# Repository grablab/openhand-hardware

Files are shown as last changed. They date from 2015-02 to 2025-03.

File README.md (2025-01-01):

Yale OpenHand Project - Hardware
=======

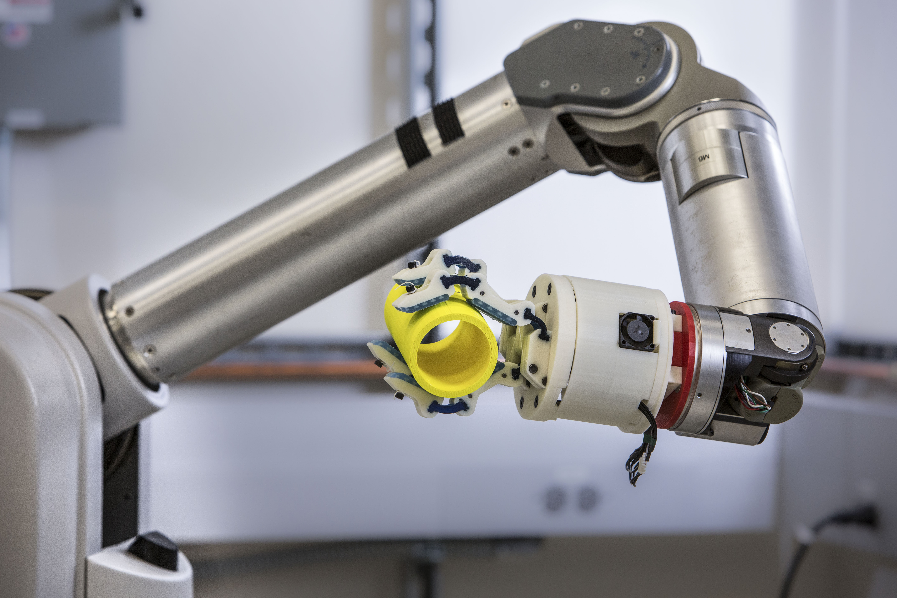
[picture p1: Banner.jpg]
Yale Openhand


CAD files for the various OpenHand hardware designs. Complete documentation, including assembly directions, can be found on the [OpenHand website](http://www.eng.yale.edu/grablab/openhand/). Control code for the most widely used hands (Model T, Model T42, Model O), with addition to a ROS node, can be found on our [openhand_node](https://github.com/grablab/openhand_node) page. For simply printing a certain hand model, navigate to the folder of the same name, and all the parts can be found in the .stl folder. For modifying the SolidWorks files, all hand-specific parts and assemblies are located inside of the hand’s folder (with exception of the M2 and VF, which share the same base as the T42). Additional parts can be found within /fingers, /couplings, or /common parts. 

All hands follow the same naming conventions with exception of Model Q. A basic dictionary of part names follows: 
a*_handName: Larger pieces used for structure. Ordered from top of the hand to the bottom. 
b*_handName: Smaller gear or servo attachment pieces. 
c*_handName: Finger mounts.
d*_handName: Optional pieces.

Most of the hand designs come with multiple finger options, each using a combination of flexure and pivot joints. Flexure joints are created with Smooth-On urethane rubber either using cut-away thin wall molds or multi-part, reusable molds. Details on Hybrid Deposition Manufacturing to create flexure joints and finger pads can be found [here](https://www.eng.yale.edu/grablab/openhand/hdm.html). 

Things to note:
- Most Solidworks parts have dependencies on other parts. To avoid warnings/errors when opening assemblies, be sure to have "Load referenced documents" set to "All" in Options>>External References
- Many of the assemblies use Configurations extensively to cut down on the number of CAD source files I have to maintain. Be sure to check them out!
- More details about our approach to CAD for this project can be found in our [CAD Guide](http://www.eng.yale.edu/grablab/openhand/OpenHand%20CAD%20Guide.pdf)

### Model T
Based on the original SDM Hand [[1]](https://www.eng.yale.edu/grablab/pubs/Dollar_IJRR2010.pdf), the Model T is the OpenHand Project's first released hand design. The four underactuated fingers are differentially coupled through a floating pulley tree, allowing for equal force output on all finger contacts. Due to the limitation of having only one actuator, this hand lacks in-hand manipulation capabilities, but excels in tasks requiring adaptable gripping with limited actuation [[2]](https://www.eng.yale.edu/grablab/pubs/Ma_RAM2017.pdf), [[3]](https://www.eng.yale.edu/grablab/pubs/Ma_ICRA2013.pdf)

### Model T42
The Model T42 is a two-finger, two-actuator hand designed for more dexterous planar tasks. It is still capable of underactuated, adaptive grasping, but the additional actuator makes it capable of some in-hand manipulation primitives as well as precision grasping, e.g. [[4]](https://www.eng.yale.edu/grablab/pubs/Calli_TASE2018.pdf), [[5]](https://www.eng.yale.edu/grablab/pubs/Sintov_RAL2019.pdf). 

### Model M2
The Model M2, short for Multi-Modality Gripper, is a minimalist gripper with a single underactuated finger and a library of modular thumb designs. Each thumb design can enable a different grasping behavior and allows for faster, more versatile design iterations. The distinct agonist and antagonist tendons allow for both underactuated and fully-actuated grasps of objects. By sacrificing the full-actuation capabilities of the M2, the Model M functions otherwise identically with only one actuator [[6]](https://www.eng.yale.edu/grablab/pubs/Ma_REMAR2015_1.pdf).

### Model VF
The Model VF, short for Variable Friction Gripper, is similar to the T42 with the addition of changing finger pad surfaces. The additional actuator within each finger allows the hand to change surface friction during manipulation. By swapping the Constant and Variable Friction fingers, the hand can translate and rotate objects in a controlled manner [[7]](http://berkcalli.com/publications/2018-SpiersCalliDollar.pdf).

### Model O
The Model O is a three-finger, four-actuator hand designed to replicate the capabilities of commercial hands such as [BarrettHand](http://www.barrett.com/robot/products-hand.htm), RightHand Robotics' [Reflex Hand](http://www.righthandrobotics.com/main:reflex), and Robotiq's 3-Finger Adaptive Gripper. Each underactuated finger is independently controlled, while a fourth actuator controls the adduction/abduction angle between two of the fingers. This allows the hand to transition between spherical-grasping and power-grasping configurations [[8]](https://www.eng.yale.edu/grablab/pubs/Odhner_IJRR2014.pdf).

### Stewart Hand
The Stewart hand is a dexterous hand designed for 6-DOF within-hand manipulation. Its non-anthropomorphic design draws inspiration from the Stewart-Gough platform parallel mechanism. This simple kinematic structure allows for straightforward, accurate control with minimal sensing [[9]](https://www.eng.yale.edu/grablab/pubs/McCann_RAM2021.pdf).

### Model Q
The Model Q is a four-finger, four-actuator hand similar in actuation elements to the Model O, but vastly different in capabilities. The two independently-actuated precision-grasp fingers allow for pinching similar to the Model T42’s capabilities. A pair of power-grasping fingers are controlled by a single actuator, while also being rotated with respect to the precision-grasping fingers by a fourth actuator. This setup enables in-hand finger-gaiting by trading control of the manipulated object between the two pairs of fingers while rotating the power-grasping set. Using its two independent sets of fingers, the hand can also manipulate an in-hand object closer to its palm for a tighter power grasp [[9]](https://www.eng.yale.edu/grablab/pubs/Ma_ROBIO2014.pdf).

### Model F3
The Model F3 is an adaptation of the flexure-flexure version of Model T42. This hand is designed to enable contact force estimation based on gripper deformation using a wrist-mounted camera. Length and angle of the finger links have been changed to avoid singularities upon contact at the fingertip. Tendon routing and motor positions are optimized to significantly reduce tendon friction which allows for more accurate force predictions. (publication under review)

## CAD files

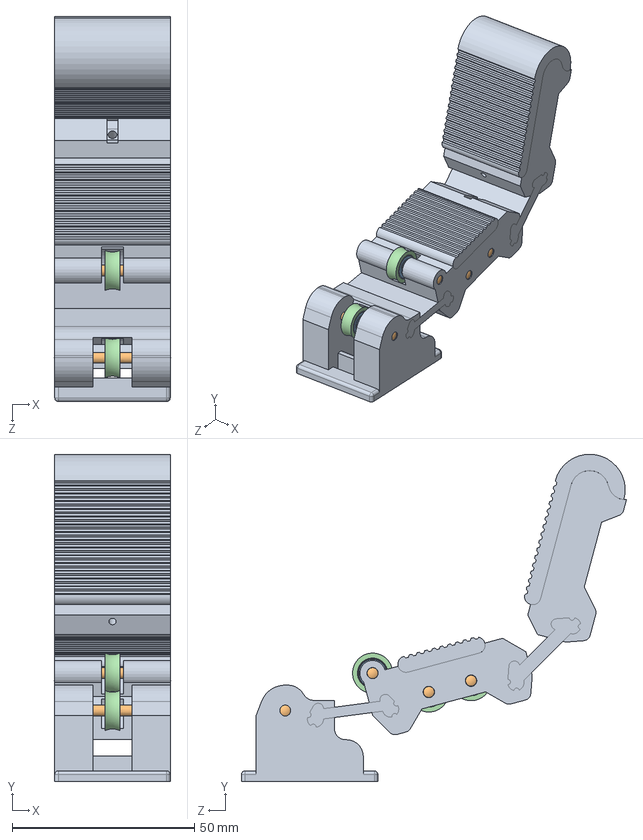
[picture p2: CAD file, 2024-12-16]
model f3 (forces-for-free hand)/F3_finger_assembly.SLDASM
32.0 x 89.9 x 105.7 mm
F3_finger
91595A138_Dowel Pin x 4
7804K126_Stainless Steel Ball Bearing x 4
bearing_sleeve x 4

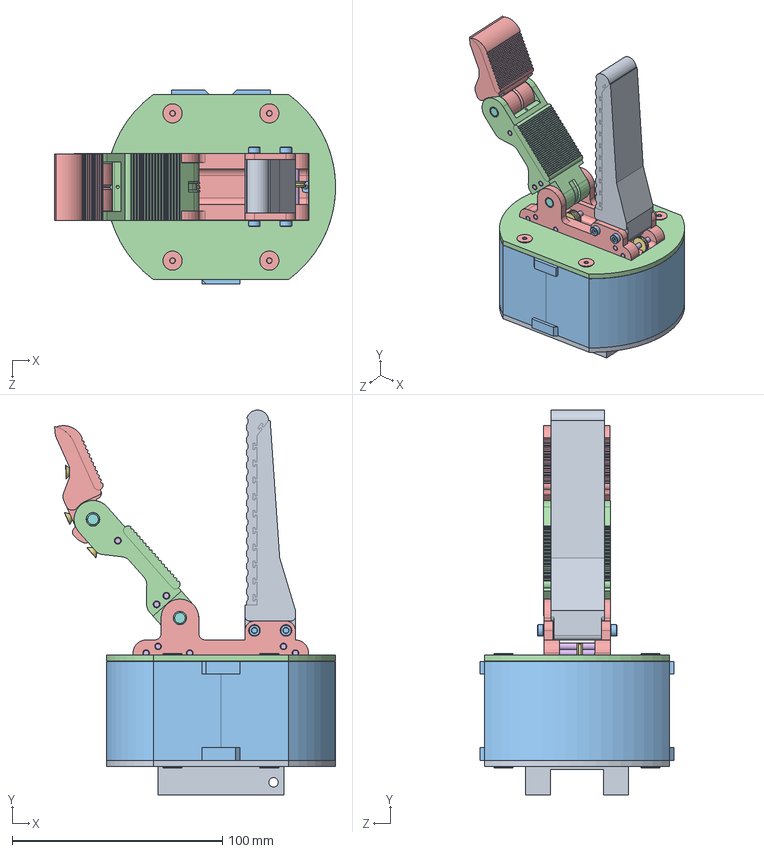
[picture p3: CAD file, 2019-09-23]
model m2/hand_m2.SLDASM
133.7 x 183.0 x 92.0 mm
a4_t42
a3_t42
a2_t42
93330A440 8-32 L3-2 standoff x 4
92210A197 8-32 L3-4 countersunk x 8
fan - 25x25x7
dynamixel XM-430 x 2
91290A012 M2 L5 socket x 4
b1_t42 x 2
d2 x 2
d1_t42_fan x 2
a1_t42
c1_m2
98381A477 D1-8 L5-4 x 8
3434T31 - nylon pulley x 4
98381A544 D1-4 L5-4 x 2
thumb1
94180A333 M3 insert x 4
91292A112 M3 L8 socket x 4
m2_pp_A
t42_pp_B
93365A120 4-40 insert x 3
91253A106 4-40 L1-4 countersunk x 3

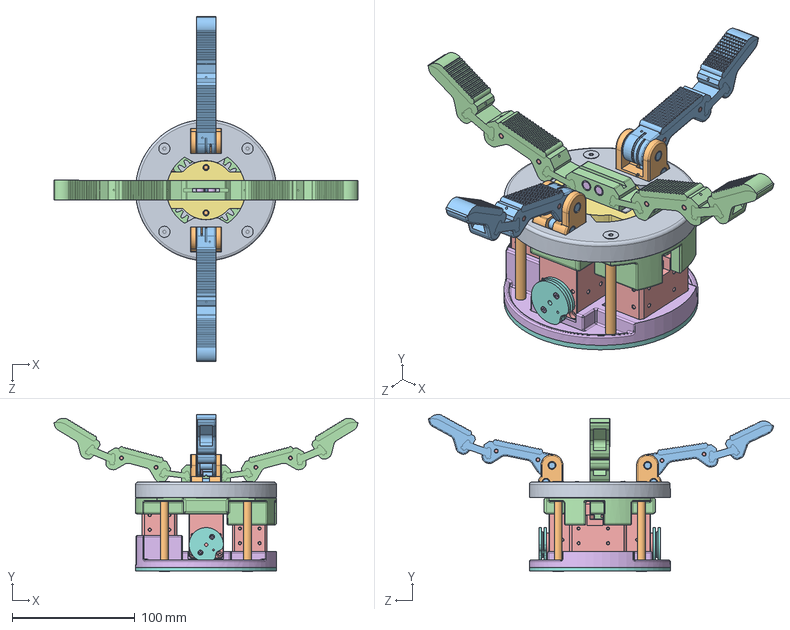
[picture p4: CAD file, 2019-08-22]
model q/hand_q.SLDASM
248.0 x 128.1 x 281.6 mm
top_outer
pivot_base x 2
98381A542 D1-4 L1 x 4
q_ffff
98381A472 D1-8 L5-8 x 8
98381A539 D1-4 L5-8 x 2
top_inner
93365A130 6-32 insert x 2
gear_main
92196A146 6-32 L3-8 socket x 2
q_pf x 2
mid_clamp
dynamixel XM-430 x 4
91290A012 M2 L5 socket x 5
gear_motor
horn2 x 2
92210A197 8-32 L3-4 countersunk x 8
93330A483 8-32 L2 standoff x 4
3434T31 - nylon pulley
pulley_block_half x 2
97395A435 D1-8 L3-8 x 3
bottom_no_bridge
bottom_reroute
bottom_brace_insertv2

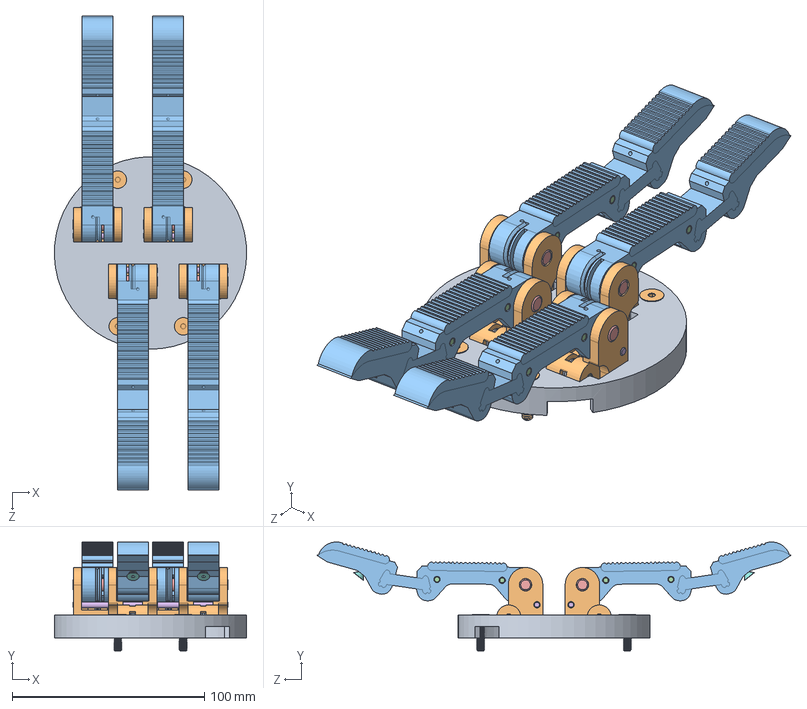
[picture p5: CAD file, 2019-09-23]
model t/MX64/block_top_pf_t.SLDASM
100.0 x 56.7 x 246.5 mm
a1_p_t
c1_t x 4
t_pf x 4
98381A472 D1-8 L5-8 x 12
98381A542 D1-4 L1 x 4
98381A475 D1-8 L1 x 4
93365A120 4-40 insert x 4
91253A106 4-40 L1-4 countersunk x 4
3434T31 - nylon pulley x 4
92210A197 8-32 L3-4 countersunk x 4

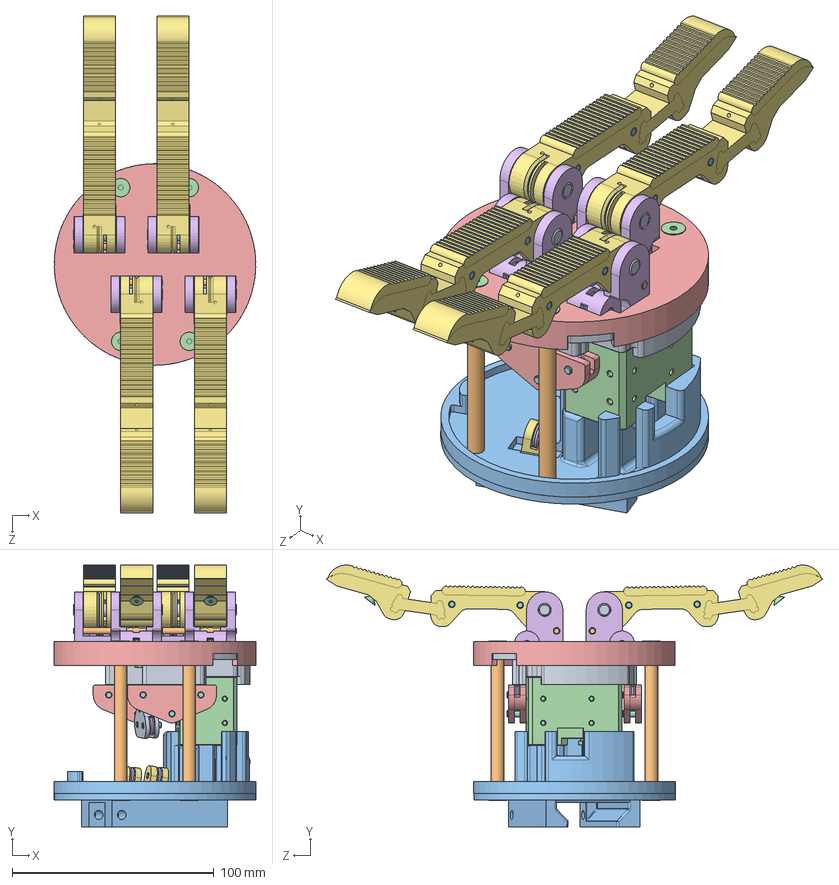
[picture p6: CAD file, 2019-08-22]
model t/XM430/hand_t_pf.SLDASM
100.0 x 129.9 x 246.5 mm
a2_t
b6_t
a3_t
dynamixel XM-430
b1_t
3434T31 - nylon pulley x 13
b2_t x 2
97395A435 D1-8 L3-8 x 11
b5_t x 2
92474A029 8-32 L5-2 standoff x 4
a4_t
92210A197 8-32 L3-4 countersunk x 8
b3_t x 4
c1_t x 4
t_pf x 4
98381A472 D1-8 L5-8 x 12
98381A542 D1-4 L1 x 4
98381A475 D1-8 L1 x 4
93365A120 4-40 insert x 4
91253A106 4-40 L1-4 countersunk x 4
a1_p_t
91290A012 M2 L5 socket x 2

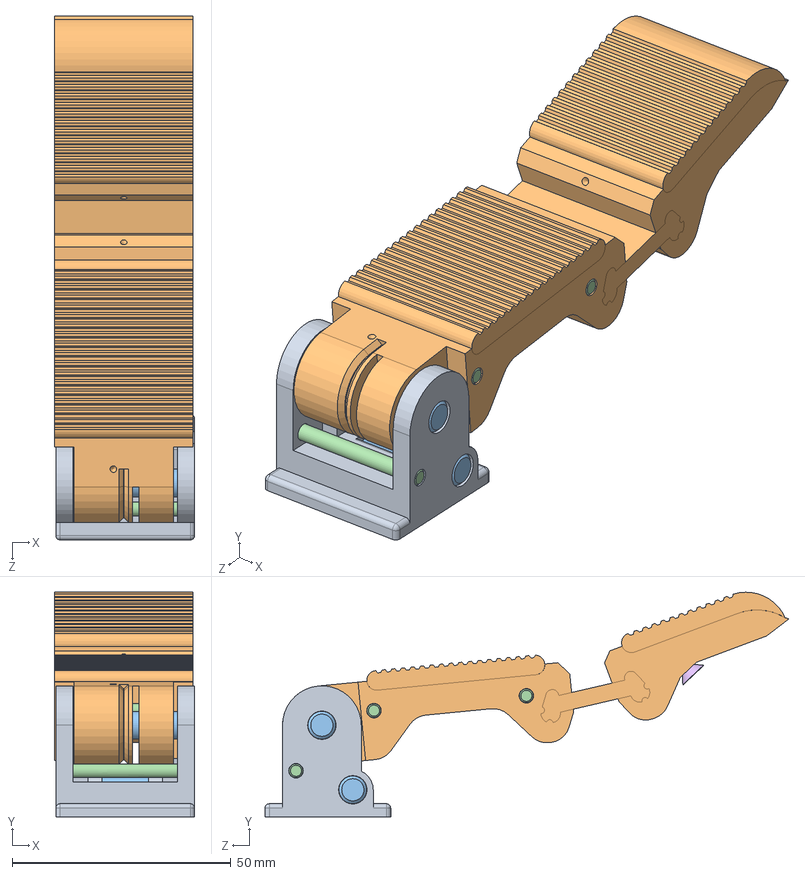
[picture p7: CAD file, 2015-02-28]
model t42/edrawings/block_finger_pf_t42.SLDASM
32.1 x 51.3 x 119.8 mm
c1_t42
finger_pf_t42
98381A544 D1-4 L5-4 x 2
98381A477 D1-8 L5-4 x 3
93365A120 4-40 insert
91253A106 4-40 L1-4 countersunk

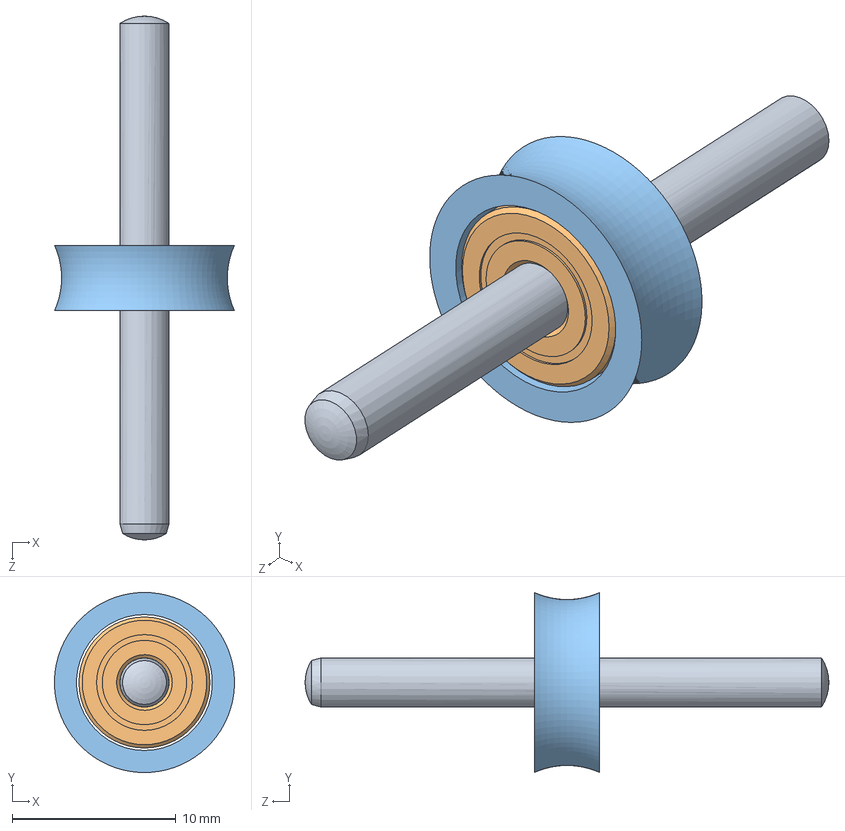
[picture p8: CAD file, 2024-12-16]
model f3 (forces-for-free hand)/sldprt/pin_bearing_assembly.SLDASM
11.0 x 11.0 x 32.0 mm
91595A138_Dowel Pin
7804K126_Stainless Steel Ball Bearing
bearing_sleeve

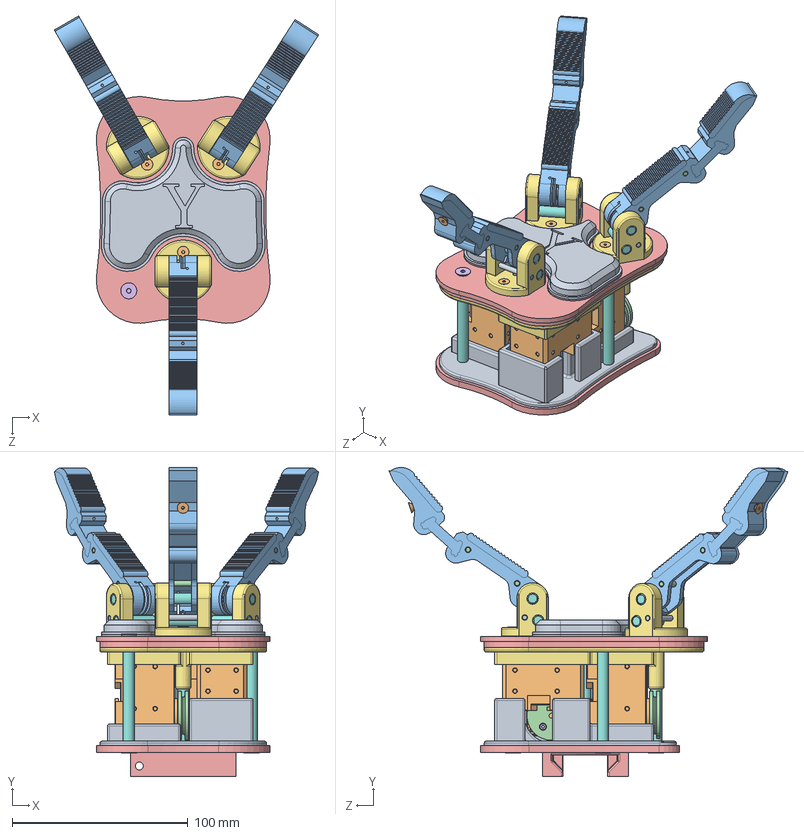
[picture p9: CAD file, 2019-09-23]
model o/XM430/hand_o_pf.SLDASM
150.6 x 176.0 x 227.2 mm
d3_o_minimal
93365A120 4-40 insert x 11
91253A110 4-40 L1-2 countersunk x 2
c2_left_o
c2_right_o
b3_o x 2
c1_o x 3
98381A544 D1-4 L5-4 x 6
98381A477 D1-8 L5-4 x 3
91253A106 4-40 L1-4 countersunk x 9
finger_pf_t x 3
98381A472 D1-8 L5-8 x 6
a1_o
92210A197 8-32 L3-4 countersunk x 8
a2_o
93330A483 8-32 L2 standoff x 4
a3_o
dynamixel XM-430 x 4
b2_o
b1_o x 3
a4_o
91290A012 M2 L5 socket x 6

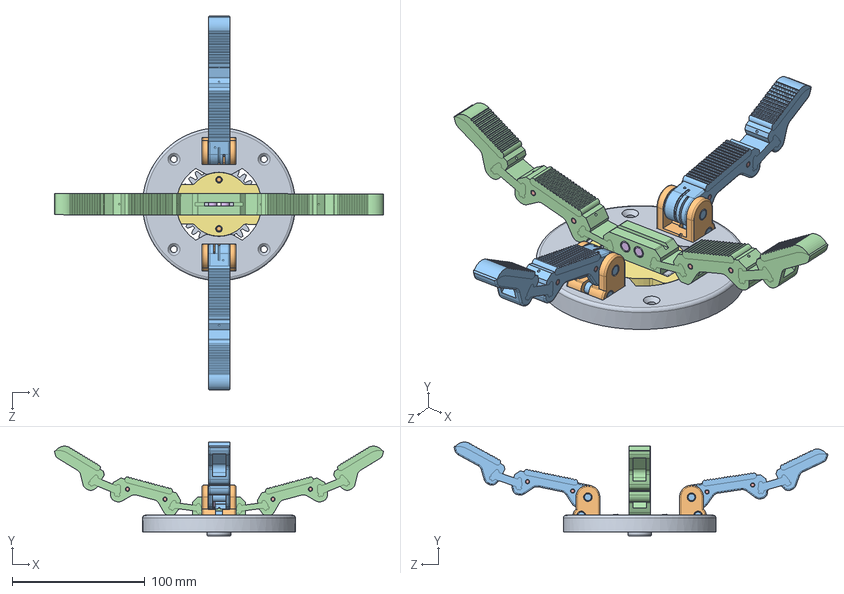
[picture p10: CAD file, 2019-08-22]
model q/asm_upper_hand.SLDASM
248.0 x 70.8 x 281.6 mm
top_outer
pivot_base x 2
98381A542 D1-4 L1 x 4
q_ffff
98381A472 D1-8 L5-8 x 8
98381A539 D1-4 L5-8 x 2
top_inner
93365A130 6-32 insert x 2
gear_main
92196A146 6-32 L3-8 socket x 2
q_pf x 2

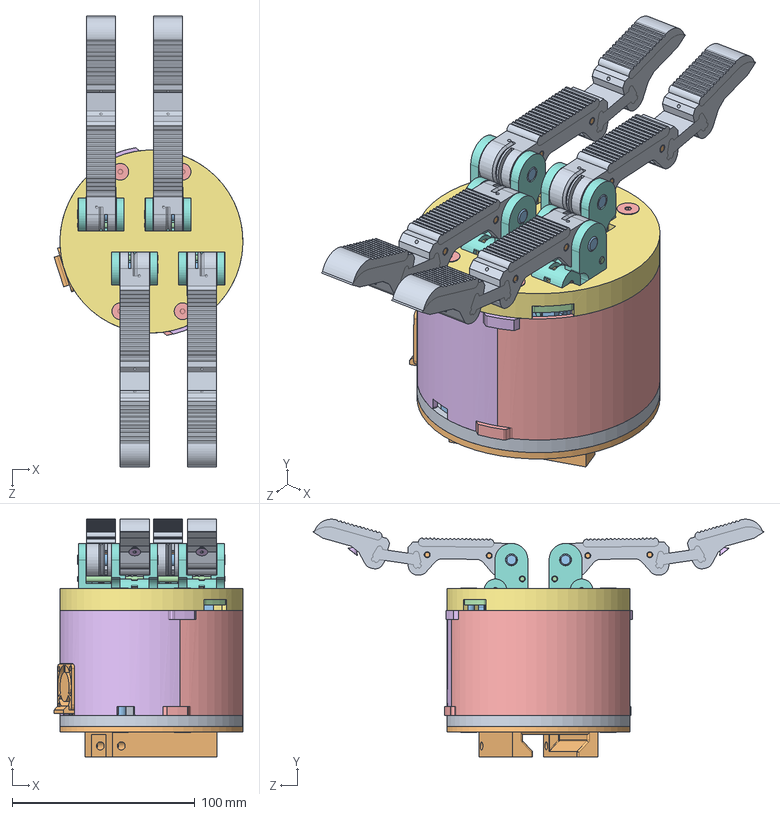
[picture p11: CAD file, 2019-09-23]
model t/MX64/hand_t.SLDASM
103.2 x 129.9 x 246.5 mm
a3_t
a4_t
92474A029 8-32 L5-2 standoff x 4
a2_t
92210A197 8-32 L3-4 countersunk x 8
b2_t x 2
3434T31 - nylon pulley x 14
97395A435 D1-8 L3-8 x 13
dynamixel-MX-64-exposed
d2_t
91772A266 2-56 L5-4 pan x 4
b1_t
91292A112 M3 L8 socket
b4_a_t
b4_b_t
92196A084 2-56 L3-4 socket x 2
90480A003 2-56 nut x 2
fan - 25x25x10
b3_t x 4
b5_t x 2
d1_a_t
d1_b_t
a1_p_t
c1_t x 4
t_pf x 4
98381A472 D1-8 L5-8 x 12
98381A542 D1-4 L1 x 4
98381A475 D1-8 L1 x 4
93365A120 4-40 insert x 4
91253A106 4-40 L1-4 countersunk x 4

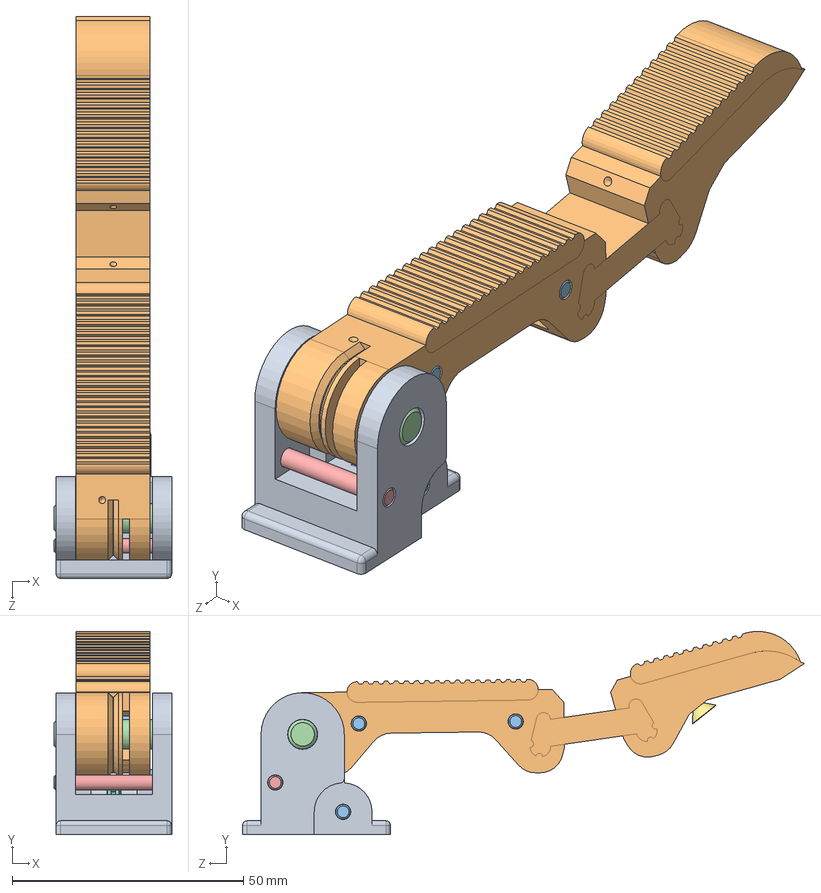
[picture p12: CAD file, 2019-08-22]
model t/XM430/block_finger_pf_t.SLDASM
25.4 x 43.9 x 121.5 mm
c1_t
t_pf
98381A472 D1-8 L5-8 x 3
98381A542 D1-4 L1
98381A475 D1-8 L1
93365A120 4-40 insert
91253A106 4-40 L1-4 countersunk
3434T31 - nylon pulley

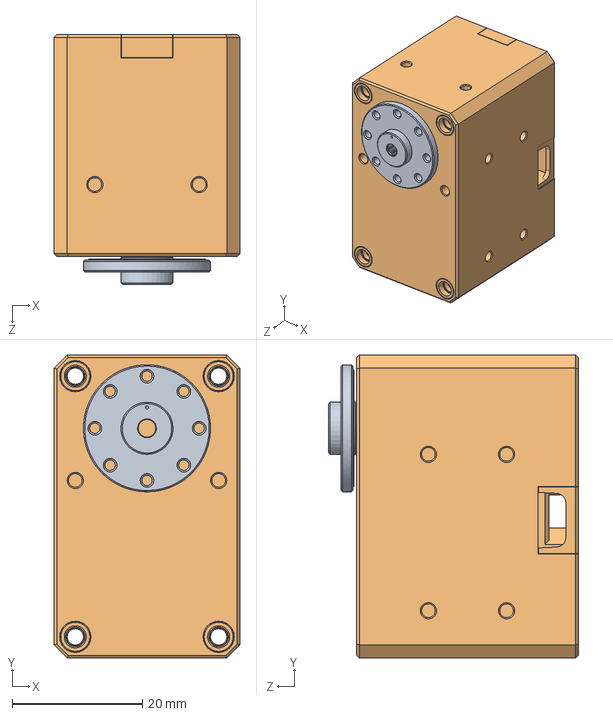
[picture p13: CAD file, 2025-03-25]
sphinx hand/Solidworks Files/Dynamixel XL-430/Dynamixel_XL-430.SLDASM
28.5 x 46.5 x 38.3 mm
HN12-N101
XL-430

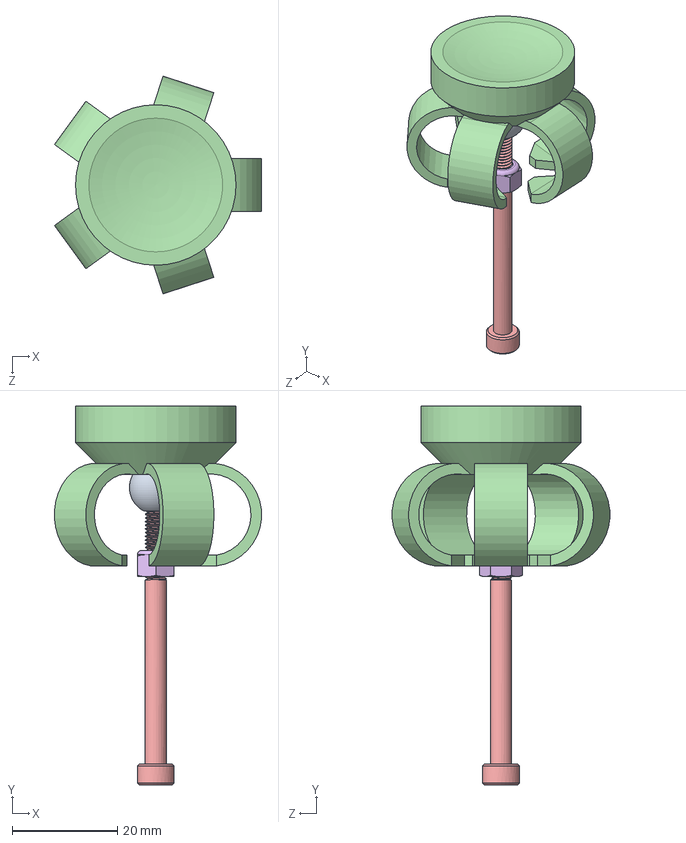
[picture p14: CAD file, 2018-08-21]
stewart hand/Solidworks Files/Finger/Fingertip/Fingertip Assembly.SLDASM
39.3 x 72.0 x 41.4 mm
Threaded Magnetic Ball - M4
90333A007 - Flanged Countersunk Washer - #6
KJ_D63_N52 - 0.375 x 0.1875 Disk Magnet
Fingerpad
91292A268 - SHCS - M4x55mm
90576A103 - Nylon Lock Nut - M4

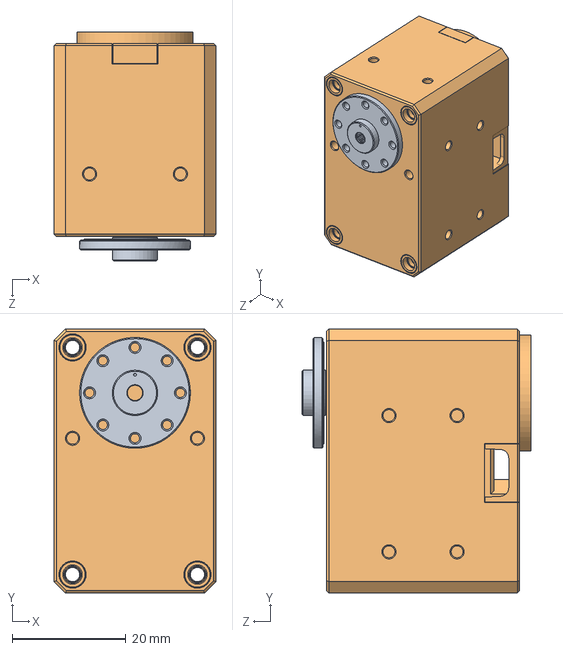
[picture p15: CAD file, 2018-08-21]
stewart hand/Solidworks Files/Palm/Dynamixel X430/XL-430.SLDASM
28.5 x 46.5 x 40.3 mm
HN12-N101
XL-430

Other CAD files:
sphinx hand/Solidworks Files/ASM_SphinxHand.SLDASM
sphinx hand/Solidworks Files/ASM_SphinxFinger.SLDASM
model o/RX28-MX28/block_finger_o.SLDASM
model t/MX64/block_finger_pf_t.SLDASM
common parts/3434T31 - nylon pulley.SLDPRT
common parts/90145A421 D1-16 L5-8.SLDPRT
common parts/90480A003 2-56 nut.SLDPRT
common parts/91253A106 4-40 L1-4 countersunk.SLDPRT
common parts/91253A110 4-40 L1-2 countersunk.SLDPRT
common parts/91253A194 8-32 L1-2 countersunk.SLDPRT
common parts/91290A012 M2 L5 socket.SLDPRT
common parts/91292A003 M2 L3 socket.SLDPRT
common parts/91292A012 M2.5 L8 socket.SLDPRT
common parts/91292A112 M3 L8 socket.SLDPRT
common parts/91294A207 M5 L8 countersunk.SLDPRT
common parts/91294A210 M5 L12 countersunk.SLDPRT
common parts/91772A266 2-56 L5-4 pan.SLDPRT
common parts/92196A084 2-56 L3-4 socket.SLDPRT
common parts/92196A146 6-32 L3-8 socket.SLDPRT
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

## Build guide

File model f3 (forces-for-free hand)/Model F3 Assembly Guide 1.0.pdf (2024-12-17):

Model F3 (Version 1.0) | Yale University Mechanical Engineering

## OpenHand

# Model F3

## Version 1.0

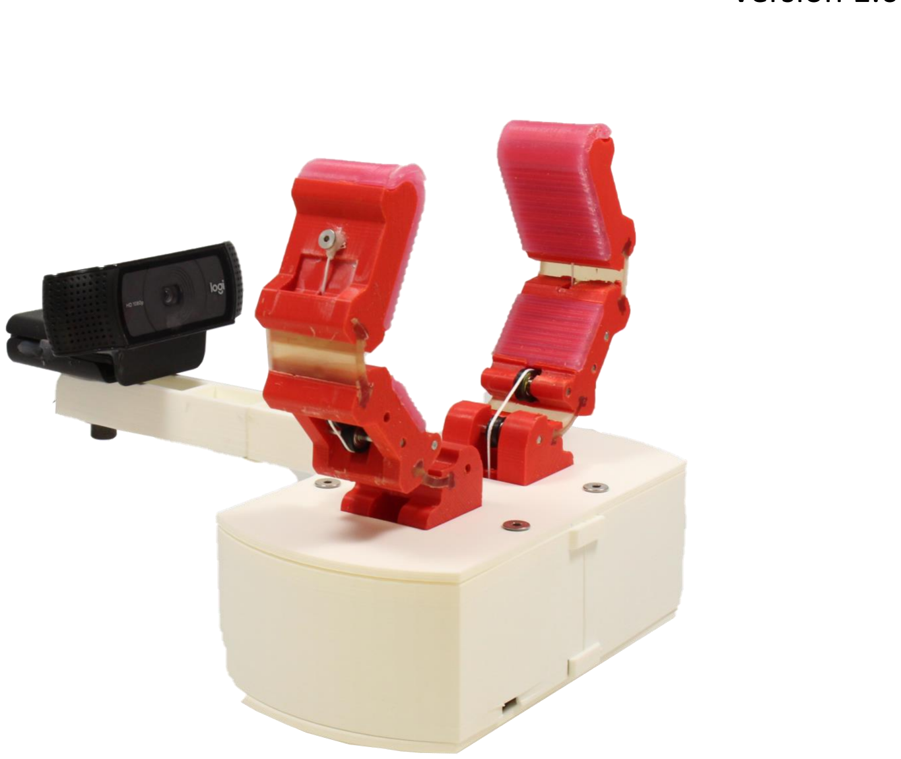
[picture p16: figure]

# Assembly Instructions

## Last updated: December 15, 2024

# Bill of Materials

Part Name | Quantity | Description | Vendor
Power Pro Spectra | 1 | Tendon | Amazon [link] (http://www.amazon.com/dp/B004TLYJZ8/ref=pe_175190_21431760_M3T1_SC_3p_dp_1)
PMC-780 Urethane | 1 | Finger Joint Urethane | Smooth-On [link] (http://www.smooth-on.com/index.php?cPath=1148)
Dragon Skin 10 Silicone | 1 | Finger Pad Urethane | Smooth-On [link] (https://www.smooth-on.com/products/dragon-skin-10-medium/)
Ø1/4”, L1-1/2”, 8-32 zinc-plated female standoff | 4 | Support | McMaster [93330A482] (http://www.mcmaster.com/#93330A482)
Ø3mm, L32mm dowel pin | 8 | Joint pin | McMaster [91595A138] (https://www.mcmaster.com/91595A138/)
Shielded stainless steel ball bearing, 3mm shaft diameter | 8 | Joint ball bearings for reducing friction | McMaster [7804K126] (https://www.mcmaster.com/7804K126/)
8-32, L3/4” countersunk bolt | 8 | Support bolt | McMaster [92210A197] (http://www.mcmaster.com/#92210a197)
M2.5, L8mm bolt | 2 | Center bolt for Dynamixel (included w/ Dynamixel) | McMaster [91292A012] (http://www.mcmaster.com/#91292a012)
M2, L5mm bolt | 4 | Mounting bolts for Dynamixel | McMaster [91290A012] (http://www.mcmaster.com/#91290a012)
4-40, L0.135” heat-set insert | 4 | Insert for bolt anchors | McMaster [93365A120] (https://www.mcmaster.com/93365A120/)
4-40, L1/4” countersunk screw | 4 | Tendon/spring anchors | McMaster [91253A106] (http://www.mcmaster.com/#91253a106)
Dynamixel XM430 | 2 | Actuator | Various [Link] (https://www.robotis.us/dynamixel-xm430-w350-t/)
Logitech C920x HD Pro Webcam | 1 | RGB Camera | Amazon[link] (https://www.amazon.com/Logitech-C920x-Pro-HD-Webcam/dp/B085TFF7M1)

* Note * There are certainly other combinations of fasteners that may work with these designs. We do not even claim that the parts list provided here is optimal for these designs. They are merely the components that we have used in past builds.

# Printed Parts List

Part Name | Quantity | Description | STL File Name
F3 finger (thin wall mold) | 2 | Fingers | F3_finger_mold.STL
a1 part 1 | 1 | Finger base with camera mount | a1_part1.STL
a1 part 2 | 1 | Extended camera mount | a1_part2.STL
a2 | 1 | Motor fixture top | a2.STL
a3 | 1 | Motor fixture bottom | a3.STL
a4 | 1 | Mount to robot arm | a4.STL
b1 | 2 | Tendon routing for motors | b1_xm_f3.STL
d1 | 2 | Case | d1.STL
Bearing sleeve | 8 | Sleeve for ball bearings to prevent tendon from slipping | bearing_sleeve.STL

# Finger Sub-Assembly

## Flexure-Flexure

Parts

F3_finger_mold.STL (x2)

PMC-780 urethane (2:1)

Dragon Skin 10 Silicone (1:1)

Refer to the OpenHand Finger Guide for more detail on casting these pads and flexures. No pins or additional elastic elements are needed for the joints in the Flexure-Flexure finger design.

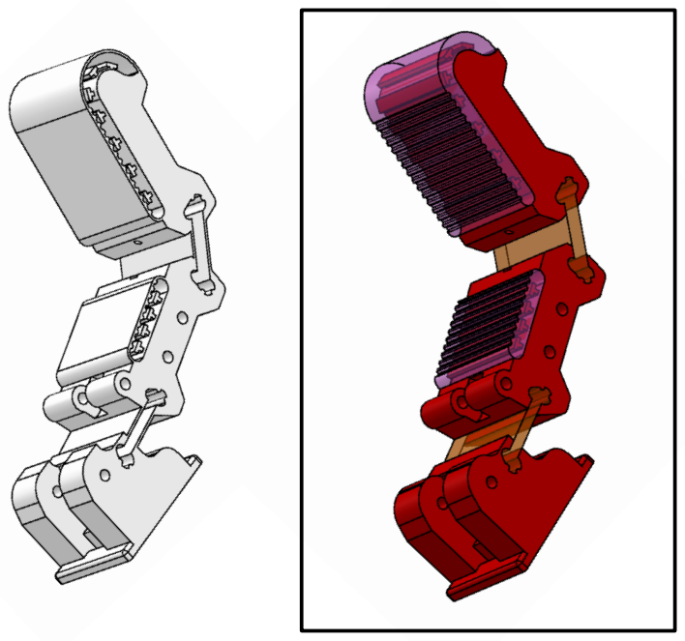
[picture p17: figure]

* Note * We printed the finger in red so that it stands out from the background. Theoretically any finger color that doesn’t blend in with the background should work fine for force estimation.

# Finger Sub-Assembly

## Flexure-Flexure

Parts

Flexure-flexure finger from page 3 (x2)

4-40, L0.135” heat-set insert (x2)

4-40, L1/4” countersunk screw (x2)

Ø3mm, L32mm dowel pin (x8)

stainless steel ball bearing (x8)

bearing sleeves (x8)

Press fit the 3mm dowel pins for tendon-rerouting into the finger links. If the pins do not press-fit easily, use a larger reamer to clean out the pin clearances or a vice. Use a soldering iron to install the heat-set insert into the distal link. The heat-set insert can be skipped in favor of using a nut for tendon termination.

The tolerance of the bearing sleeve may come out differently from different printers. Test print and change the size of the inner sleeve to find out what would achieve a press or loose fit. Fix sleeve relative to outer bearing using super glue if necessary.

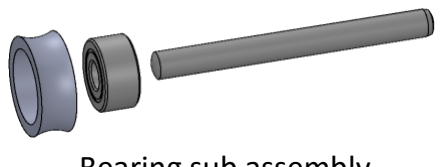
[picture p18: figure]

Bearing sub assembly

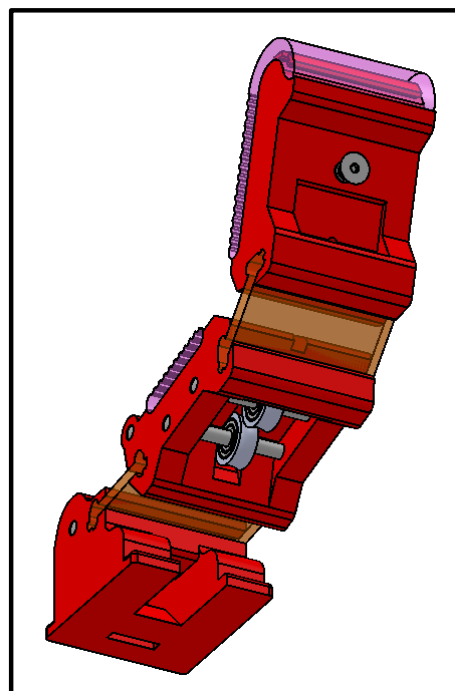
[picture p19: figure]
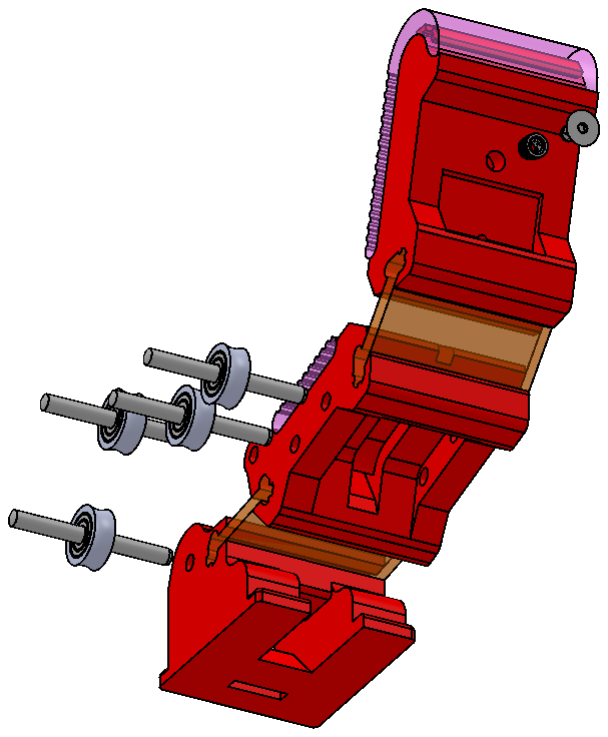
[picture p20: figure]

# Finger Sub-Assembly

## Flexure-Flexure

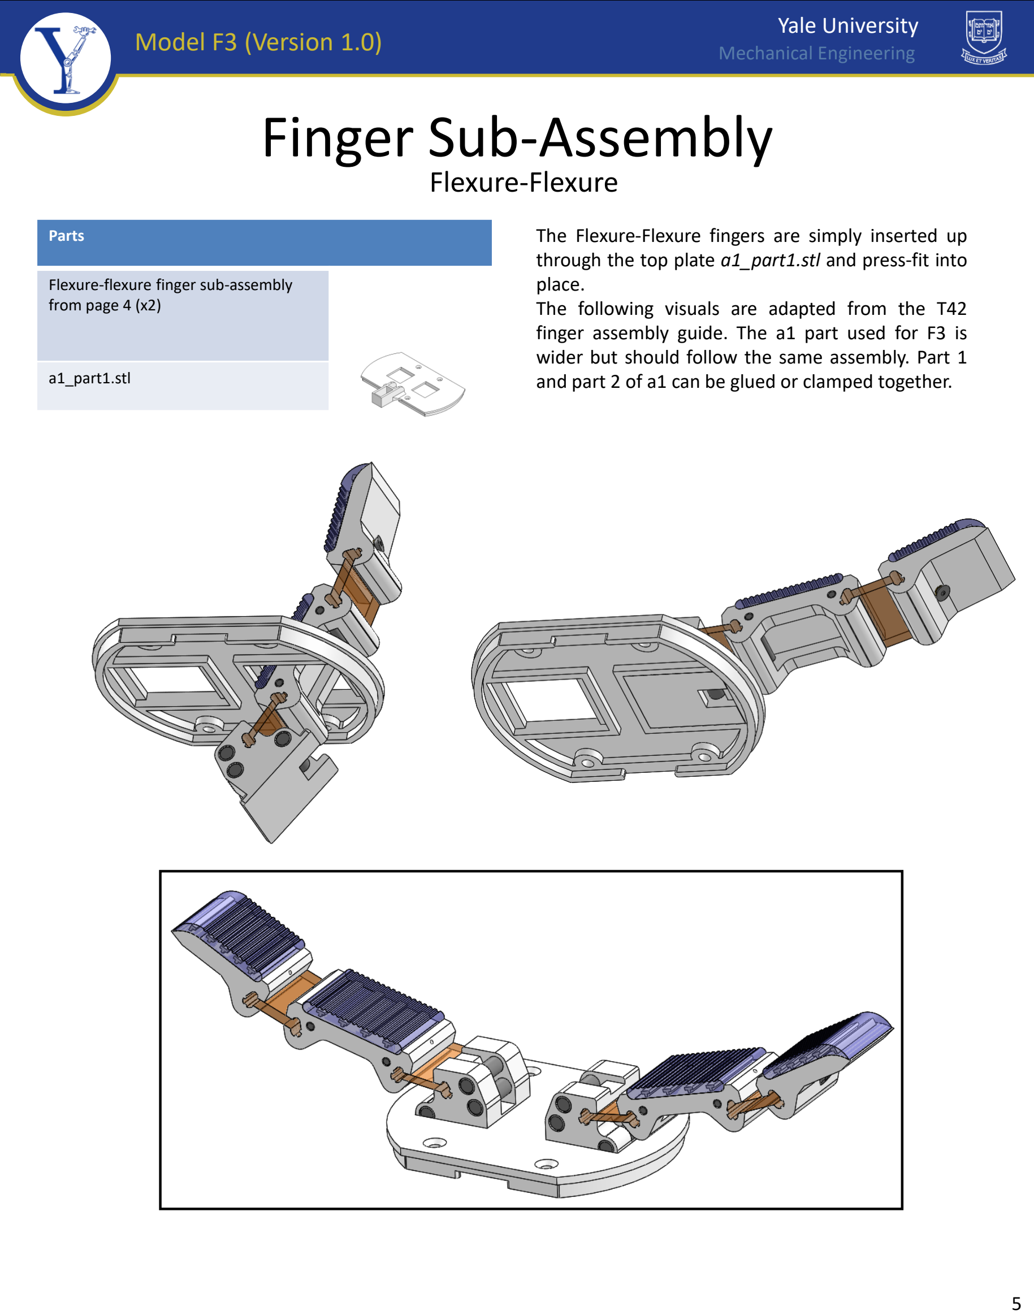
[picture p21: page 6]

Parts

Flexure-flexure finger sub-assembly from page 4 (x2)

a1_part1.stl

The Flexure-Flexure fingers are simply inserted up through the top plate a1_part1.stl and press-fit into place.
The following visuals are adapted from the T42 finger assembly guide. The a1 part used for F3 is wider but should follow the same assembly. Part 1 and part 2 of a1 can be glued or clamped together.

# Actuator Sub-Assembly

Parts

Dynamixel XM430 (x2)

b1_xm_f3.stl (x2)

Spectra tendon line

M2.5, L8mm bolt (x2)

M2, L5mm bolt (x4)

## Dynamixel

Tie about a foot (~30cm) of tendon line to the servo pulley b1_dynamixel_t42.stl through the non-bolt hole. It’s a good idea to wire the two Dynamixels together in a daisy-chain setup in this step.

The following final assembly is adapted from the T42 assembly guide. The middle-printed part is no longer needed and the Dynamixels should fit directly between parts a3 and a4.

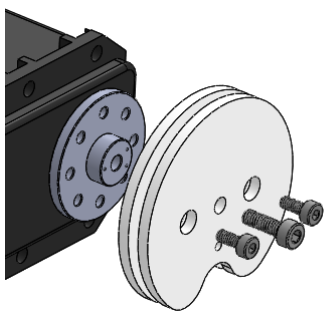
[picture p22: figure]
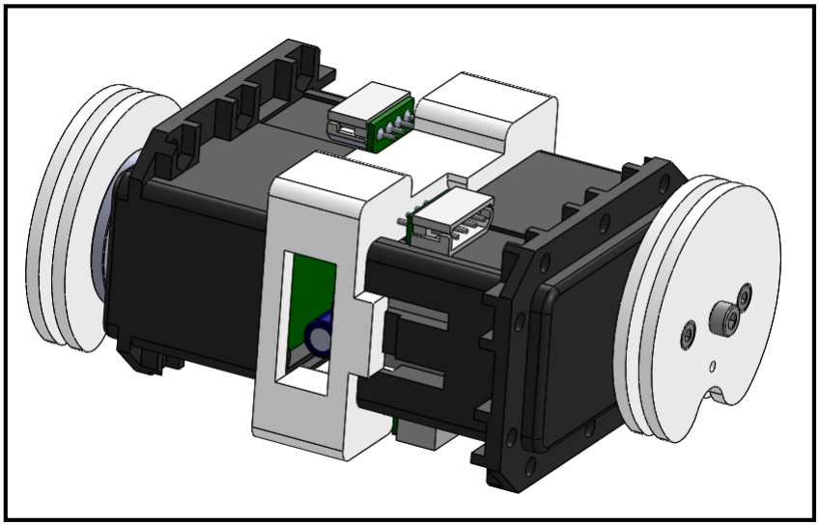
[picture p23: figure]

# Actuator Sub-Assembly

## Dynamixel

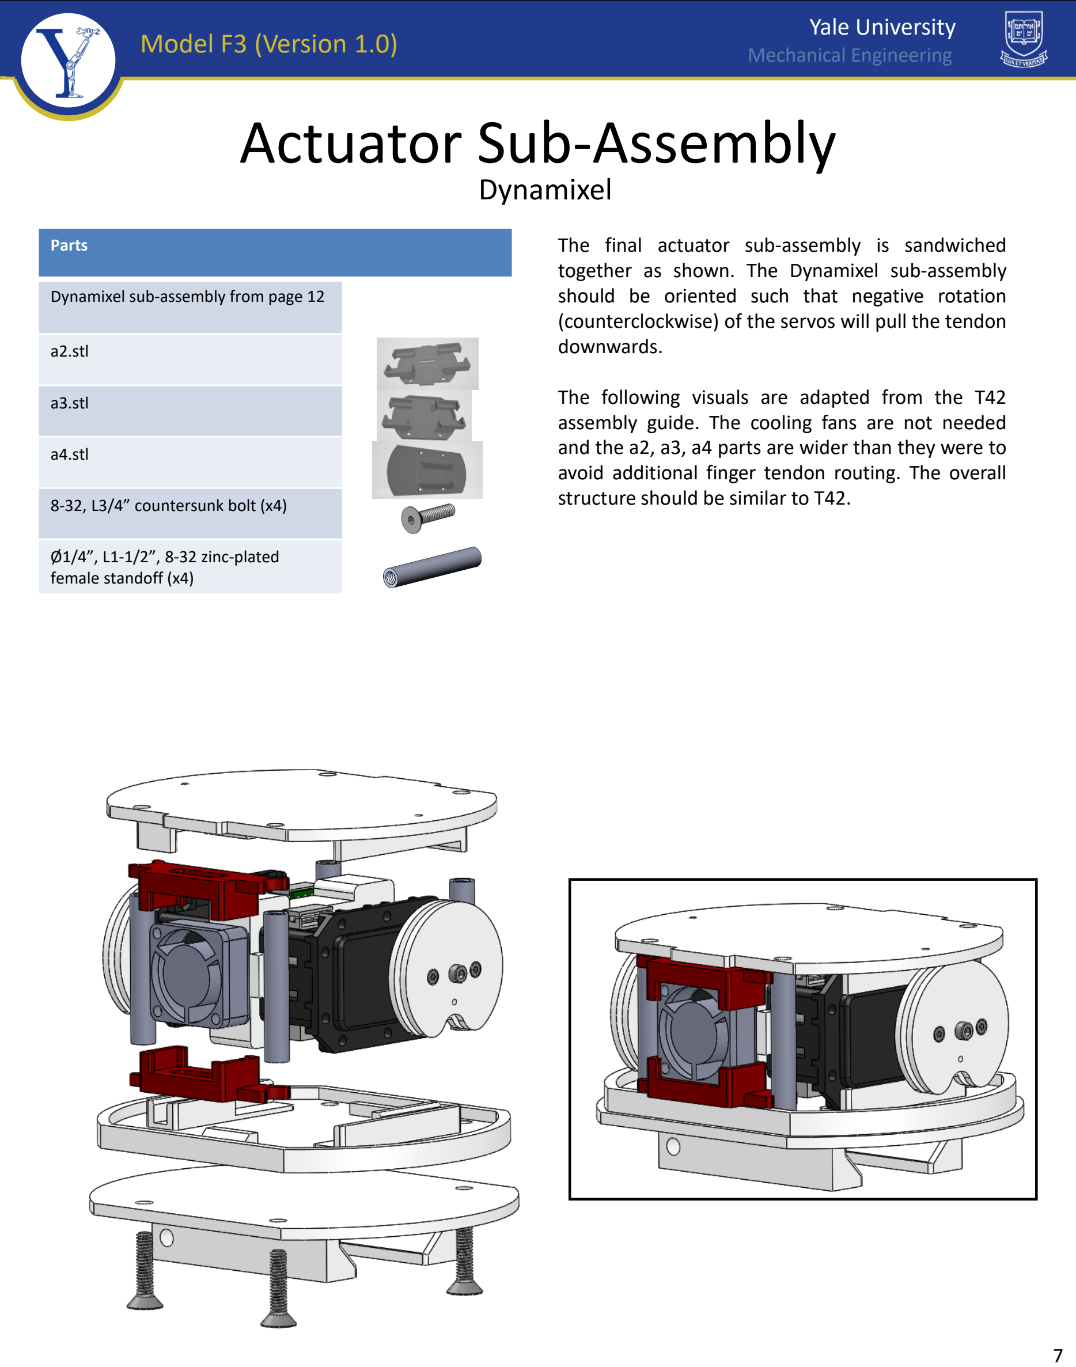
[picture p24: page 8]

Parts

Dynamixel sub-assembly from page 12

a2.stl

a3.stl

a4.stl

8-32, L3/4” countersunk bolt (x4)

Ø1/4”, L1-1/2”, 8-32 zinc-plated female standoff (x4)

The final actuator sub-assembly is sandwiched together as shown. The Dynamixel sub-assembly should be oriented such that negative rotation (counterclockwise) of the servos will pull the tendon downwards.

The following visuals are adapted from the T42 assembly guide. The cooling fans are not needed and the a2, a3, a4 parts are wider than they were to avoid additional finger tendon routing. The overall structure should be similar to T42.

# Final Assembly

Parts

Actuator sub-assembly (Dynamixel) from page 7

Top flexure-base sub-assembly from page 5

8-32, L3/4” countersunk bolt (x4)

d1.stl (x2, optional)

The top sub-assembly with topmost plate and the fingers are assembled onto the actuator sub-assembly in the same way, no matter which fingers are used. Use the 4 countersunk 8-32 bolts to sandwich and secure all the parts together.

## Hand Frame

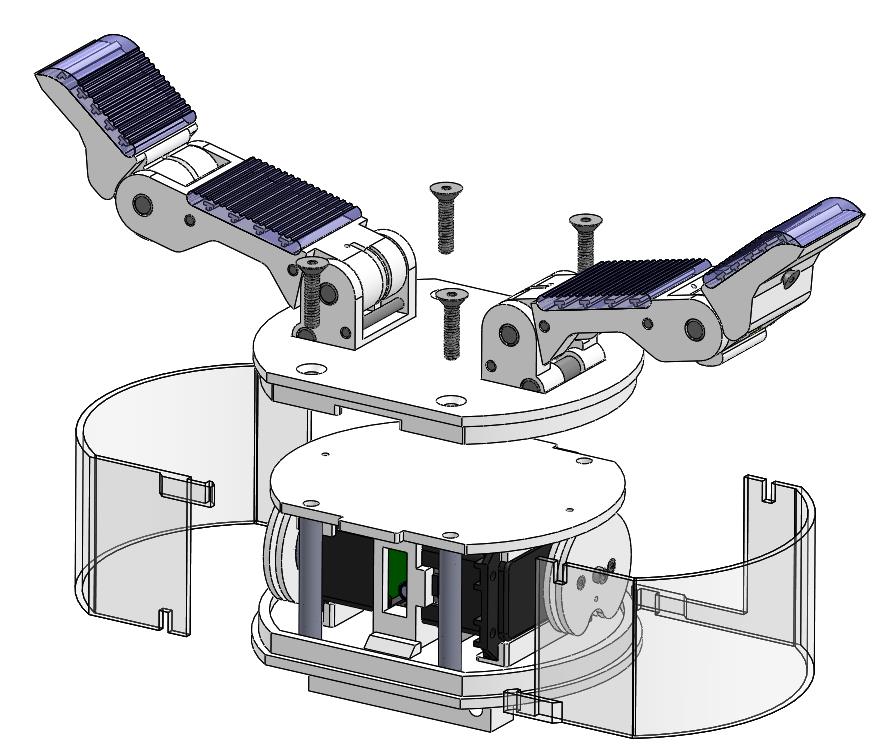
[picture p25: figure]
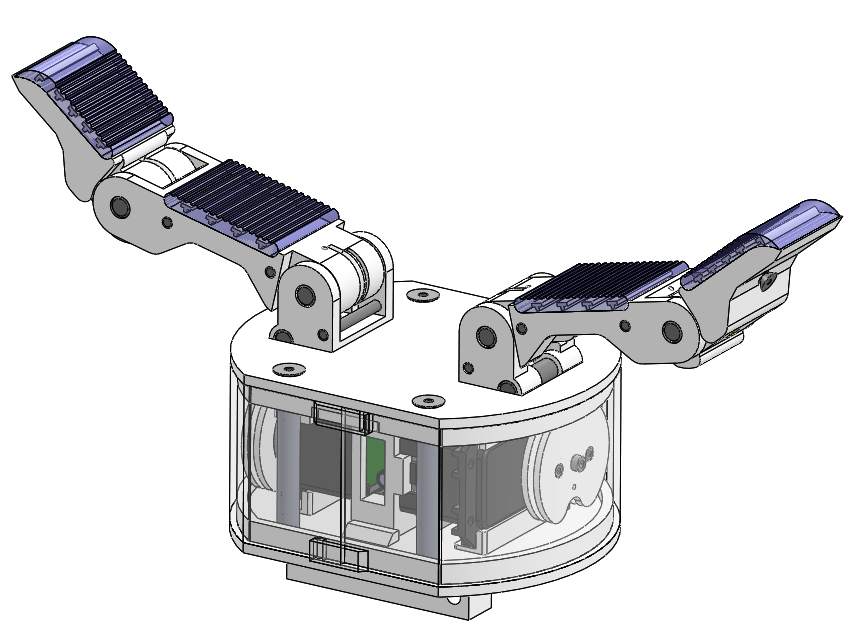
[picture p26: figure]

# Final Assembly

Parts

Hand assembly

Spectra tendon line

## Tendon Routing

The tendon is routed from the servo pulley through the tendon clearance. The tendon is routed for each finger as shown below. The tendons will run over the ball bearings on the dowel pins.

The tendon can be terminated on the bolt at the back of the distal finger link or with a nut right after the tendon exits the back of the finger.

To zero the tendon line:
1. Anchor the tendon
2. Hook up the actuator and command it to its zero position
3. Unscrew the pulley until it can spin freely
4. Rotate the pulley until the tendon line is taut
5. Re-secure the drive pulley to the actuator

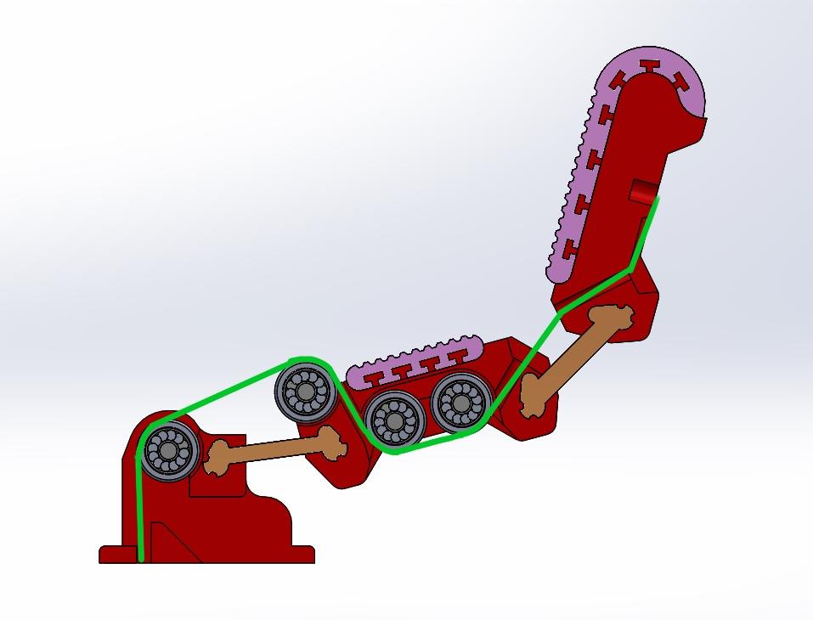
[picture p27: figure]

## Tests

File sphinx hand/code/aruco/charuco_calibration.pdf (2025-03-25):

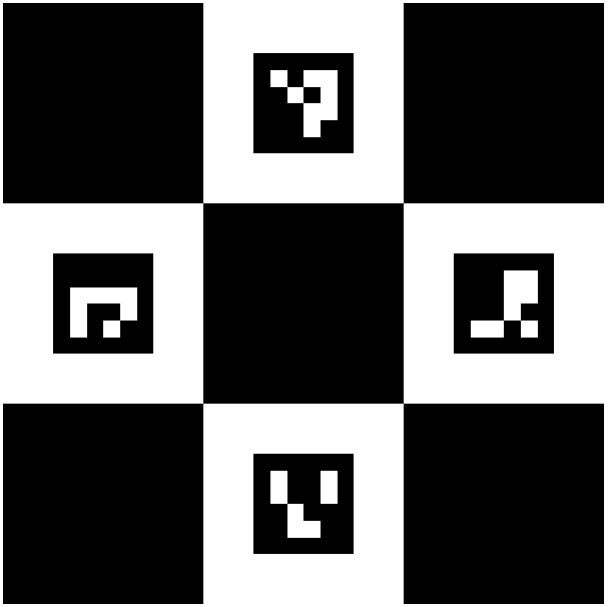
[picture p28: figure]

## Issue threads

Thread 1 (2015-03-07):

PMC-780 Urethane for M2 - dry or wet?

dylanvaughn, 2015-03-07:
Hello - in the M2 BOM it says PMC-780 Urethane - on the provided link:

http://www.smooth-on.com/index.php?cPath=1148

there are two options - wet or dry - which should be purchased?

Thanks, Dylan

jessewalton, 2015-03-08:
You want DRY. The wet is used for molding concrete.

dylanvaughn, 2015-03-08:
OK that's what I thought just wanted to be sure - thanks!

grablab, 2015-03-10:
Just to confirm, dry! I'll update the documentation for clarification. Thanks!

jbohren, 2015-03-10:
> Just to confirm, dry! I'll update the documentation for clarification. Thanks!

Are docs in source control too somewhere, or are they only on the project website?

grablab, 2015-03-10:
Project website. I can add them to the source control too.

jbohren, 2015-03-10:
> Project website. I can add them to the source control too.

If they're in tex or something that would be really cool, and make it easy to contribute fixes like this.

Closed 2015-03-08.

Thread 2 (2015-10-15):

STL Files

ddworken, 2015-10-15:
In the README.md it says that stl files are available but I do not see them anywhere in the folder for Common Parts. If you still have them available I would really appreciate it if could you upload them.

grablab, 2015-10-15:
@ddworken , we never generated stl or step files for the common parts, since no one had ever expressed a need for them. The stl files for the fasteners can be found directly from the McMaster site if you look up the part number. I believe the stl's for the servo's can be found online off of vendor sites as well. You could also upload the .sldprt to Onshape and re-export as stl/step from there. If you're having trouble w/ those options, send me an email (from the project website) directly, and I'll get you the stl's you need.

Closed 2015-10-15.

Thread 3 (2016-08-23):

d2_t42.STL and d2_power_t42.STL are the same file.

JosepVirgili, 2016-08-23:
The d2_t42.STL and d2_power_t42.STL are the same file and thus the Dynamixel fan does not fit.  The same happens with the STEP files.

The SLDPRT contains both versions.

Closed 2021-03-24.

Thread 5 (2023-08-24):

Finger_ffff_q.stl not same as part

redbarn7, 2023-08-24:
It looks to me like the STL file was shortened to fit in a printer.  I will work on making a version that is symmetric.  But also thinking about breaking it into two pieces.  In any event, the current part is asymmetrical and will probably not work as intended.

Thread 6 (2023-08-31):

Cannot change the CAD parameters (e.g., link length)

pazeshun, 2023-08-31:
I want to change the CAD parameters of Model O.
I read https://www.eng.yale.edu/grablab/openhand/OpenHand%20CAD%20Guide.pdf and changed a parameter value in the Design Table, but it was not reflected.

## What I did
1. With SOLIDWORKS2022, open https://github.com/grablab/openhand-hardware/blob/8ae3f2155dde6066edb39cbd29b1b716d7b0f7df/model%20o/RX28-MX28/hand_o.SLDASM
   - While opening, I had to specify my local path to https://github.com/grablab/openhand-hardware/blob/8ae3f2155dde6066edb39cbd29b1b716d7b0f7df/params_print.SLDPRT
2. Open https://github.com/grablab/openhand-hardware/blob/8ae3f2155dde6066edb39cbd29b1b716d7b0f7df/fingers/t_pp_A.SLDPRT
3. Open https://github.com/grablab/openhand-hardware/blob/8ae3f2155dde6066edb39cbd29b1b716d7b0f7df/fingers/params_finger_t.SLDPRT
4. Open the Design Table of `params_finger_t.SLDPRT`
5. Change `length ratio (Ld/Lp)` to 1.0
6. Close the Design Table
7. Switch to the window of `t_pp_A.SLDPRT`

## What I faced
- Rebuilding of `t_pp_A.SLDPRT` failed with errors and the changed parameter was not reflected:
  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
- When I checked the Equations of `t_pp_A.SLDPRT`, I found many errors. I assume this is the cause, but I'm not sure how to fix them:
  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

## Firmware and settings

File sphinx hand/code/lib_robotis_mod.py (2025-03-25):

#!/usr/bin/python
#
# Copyright (c) 2009, Georgia Tech Research Corporation
# All rights reserved.
#
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

## Controlling Robotis Dynamixel RX-28 & RX-64 servos from python
## using the USB2Dynamixel adaptor.

## Authors: Travis Deyle, Advait Jain & Marc Killpack (Healthcare Robotics Lab, Georgia Tech.)

##MOD VERSION: 2013, some additional modifications made to make appropriate for both MX/RX series (Raymond R. Ma)
##MOD VERSION: 2018,2019, additions for python3, searching for dynamixels, and readdressing now available (Andrew Morgan)
##                   Additional Changes for Robotis_Servo_X for all readings of new dynamixels.
##MOD VERSION: 2020, additions for XL series servos (Walter G. Bircher)

from __future__ import print_function
import serial
import time
import _thread
import sys, optparse
import math
import random
import ctypes
import numpy as np
import IPython

from registerDict import *
import registerDict


class USB2Dynamixel_Device():
    ''' Class that manages serial port contention between servos on same bus
    '''
    def __init__( self, dev_name = '/dev/ttyUSB0', baudrate = 57142):
        try:
            self.dev_name = string.atoi( dev_name ) # stores the serial port as 0-based integer for Windows
        except:
            self.dev_name = dev_name # stores it as a /dev-mapped string for Linux / Mac

        self.mutex = _thread.allocate_lock()	#helps ensure that only a single port is used?
        self.servo_dev = None

        self.acq_mutex()
        self._open_serial( baudrate )
        self.rel_mutex()

    def acq_mutex(self):
        self.mutex.acquire()

    def rel_mutex(self):
        self.mutex.release()

    def send_serial(self, msg):
        # It is up to the caller to acquire / release mutex
        self.servo_dev.flushInput()		#added to remove extra bytes from input buffer
        byte_msg = bytearray(msg)
        sent = self.servo_dev.write(byte_msg)


    def read_serial(self, nBytes=1):
        # It is up to the caller to acquire / release mutex 

        rep = self.servo_dev.read( nBytes )
        return rep

    def _open_serial(self, baudrate):
        try:
            self.servo_dev = serial.Serial(self.dev_name, baudrate, timeout=1.0)
            # Closing the device first seems to prevent "Access Denied" errors on WinXP
            # (Conversations with Brian Wu @ MIT on 6/23/2010)
            self.servo_dev.close()
            self.servo_dev.parity = serial.PARITY_NONE
            self.servo_dev.stopbits = serial.STOPBITS_ONE
            self.servo_dev.open()

            self.servo_dev.flushOutput()
            self.servo_dev.flushInput()

        except (serial.serialutil.SerialException) as e:
            raise RuntimeError('lib_robotis: Serial port not found!\n')
        if(self.servo_dev == None):
            raise RuntimeError('lib_robotis: Serial port not found!\n')

##################################################################################################

#Class for Model RX and MX Servos

##################################################################################################
class Robotis_Servo():
    ''' Class to use a robotis RX-28 or RX-64 servo.
    '''
    def __init__(self, USB2Dynamixel, servo_id, series = None ):
        ''' USB2Dynamixel - USB2Dynamixel_Device object to handle serial port.
                            Handles threadsafe operation for multiple servos
            servo_id - servo ids connected to USB2Dynamixel 1,2,3,4 ... (1 to 253)
                       [0 is broadcast if memory serves]
            series - Just a convenience for defining "good" defaults on MX series.
                     When set to "MX" it uses these values, otherwise it uses values
                     better for AX / RX series.  Any of the defaults can be overloaded
                     on a servo-by-servo bases in servo_config.py.
        '''

        self.series = series;	#record dynamixel series
        self.return_delay = 250 * 2e-6	#default return delay
        # To change the defaults, load some or all changes into servo_config.py
        if series == 'MX':			#MX series generally has 4x the travel and maximums of RX
            defaults = {
                'home_encoder': 0x7FF,
                'max_encoder': 0xFFF,
                'rad_per_enc': math.radians(360.0) / 0xFFF,
                'max_ang': math.radians(180),
                'min_ang': math.radians(-180),
                'flipped': False,
                'max_speed': math.radians(100)
                }
        else: # Common settings for RX-series.  Can overload in servo_config.py
            defaults = {
                'home_encoder': 0x200,
                'max_encoder': 0x3FF,  # Assumes 0 is min.
                'rad_per_enc': math.radians(300.0) / 1024.0,
                'max_ang': math.radians(148),
                'min_ang': math.radians(-148),
                'flipped': False,
                'max_speed': math.radians(100)
                }
        self.ADDR_DICT = registerDict.RXMX_Series

        # Error Checking
        if USB2Dynamixel == None:
            raise RuntimeError('lib_robotis: Robotis Servo requires USB2Dynamixel!\n')
        else:
            self.dyn = USB2Dynamixel
            self.dyn.servo_dev.flush()

        # ID exists on bus?
        self.servo_id = servo_id

        try:
            self.read_address(self.ADDR_DICT["ADDR_ID"])
        except Exception as inst:
            raise RuntimeError('lib_robotis: Error encountered.  Could not find ID (%d) on bus (%s), or USB2Dynamixel 3-way switch in wrong position.\n' %
                               ( servo_id, self.dyn.dev_name ))

        # Set Return Delay time - Used to determine when next status can be requested
        data = self.read_address( self.ADDR_DICT["ADDR_RETURN_DELAY_TIME"], 1)
        self.return_delay = data[0] * 3e-4

        self.settings = {}
        #removed external servo settings file to simplify things (we usually only deal with MX or RX, and both settings are included above)
        # Set to default any parameter not specified in servo_config
        for key in defaults.keys():
            if key in self.settings: ##CHANGED self.settings.has_key( key ) THIS SHOULD ALSO WORK IN PYTHON2
                pass
            else:
                self.settings[ key ] = defaults[ key ]	#defaults dict moved into settings component


    def init_cont_turn(self):
        '''sets CCW angle limit to zero and allows continuous turning (good for wheels).
        After calling this method, simply use 'set_angvel' to command rotation.  This
        rotation is proportional to torque according to Robotis documentation.
        '''
        self.write_address(self.ADDR_DICT["ADDR_CCW_ANGLE_LIMIT_L"], [0,0])

    #UPDATED: set limits based on servo max encoder, reset speed to 0
        #should work properly for both RX/MX series
    def kill_cont_turn(self):
        '''resets CCW angle limits to allow commands through 'move_angle' again
        '''
        max_encoder = self.settings['max_encoder']
        hi,lo = int(max_encoder / 256), int(max_encoder % 256)	#addition made to reset encoder appropriately for both series
        self.write_address(self.ADDR_DICT["ADDR_CCW_ANGLE_LIMIT_L"], [lo,hi])

    def is_moving(self):
        ''' returns True if servo is moving.
        '''
        data = self.read_address( self.ADDR_DICT["ADDR_MOVING"], 1 )
        return data[0] != 0

    def read_voltage(self):
        ''' returns voltage (Volts)
        '''
        data = self.read_address( self.ADDR_DICT["ADDR_PRESENT_VOLTAGE"], 1 )
        return data[0] / 10.

    def read_temperature(self):
        ''' returns the temperature (Celcius)
        '''
        data = self.read_address( self.ADDR_DICT["ADDR_PRESENT_TEMPERATURE"], 1 )
        return data[0]

    def read_load(self):
        ''' number proportional to the torque applied by the servo.
            sign etc. might vary with how the servo is mounted.
        '''
        data = self.read_address( self.ADDR_DICT["ADDR_PRESENT_LOAD_L"], 2 )
        load = data[0] + data[1] * 256
        if load>1024:
            return 1024-load
        else:
            return load

    #ADDED: current functionality only available for MX-64 series:
    def read_current(self):
        if self.series=='MX':
            data = self.read_address( self.ADDR_DICT["ADDR_CURRENT_L"], 2 )	#current spans addresses 0x44 and 0x45
            curr = data[0] + data[1] * 256
            return 4.5*(curr-2048)		#in mA
        else:
            return 0.

    #ADDED: speed address same for both MX/RX series
    def read_speed(self):
        data = self.read_address( self.ADDR_DICT["ADDR_PRESENT_SPEED_L"], 2 )
        speed = data[0] + data[1] * 256
        if speed>1024:
            return float(1024-speed)/1024.0
        else:
            return float(speed)/1024.0

    #both moving speed in joint mode (between designated positions) as well as wheel mode (which only sets direction in operation)
    def apply_speed(self,amnt):
        amnt = max(0.,min(abs(amnt),1.0))
        speed_val = int(amnt*1023)
        if speed_val < 0:
            speed_val = speed_val+1024
        hi,lo = int(speed_val / 256), int(speed_val % 256)
        self.write_address(self.ADDR_DICT["ADDR_MOVING_SPEED_L"],[lo,hi])

    def read_encoder(self):
        ''' returns position in encoder ticks
        '''
        data = self.read_address( self.ADDR_DICT["ADDR_PRESENT_POSITION_L"], 2 )
        enc_val = data[0] + data[1] * 256
        return enc_val

    def read_target_encoder(self):
        data = self.read_address( self.ADDR_DICT["ADDR_GOAL_POSITION_L"], 2 )
        enc_val = data[0] + data[1] * 256
        return enc_val

    def read_angle(self):	#based entirely off of the encoder setting
        ''' returns the current servo angle (radians)
        '''
        ang = (self.read_encoder() - self.settings['home_encoder']) * self.settings['rad_per_enc']
        if self.settings['flipped']:
            ang = ang * -1.0
        return ang

    #ADDED: reading/setting the max torque output (at different addresses)
    def read_max_torque(self):	#set twice, but we'll read the first instance
        data = self.read_address( self.ADDR_DICT["ADDR_MAX_TORQUE_L"], 2 )
        torque = data[0] + data[1] * 256
        return torque

    def apply_max_torque(self,val):	#unlike speed, 0 is not max torque; no mode dependencies to use/set
        amnt = max(0.,min(abs(val),1.0))
        n = int(amnt*1023)
        n = min(max(n,0), 1023)		#no scaling issues between MX and RX like with position
        hi,lo = int(n / 256), int(n % 256)
        self.write_address( 0x22, [lo,hi])
        return self.write_address( self.ADDR_DICT["ADDR_MAX_TORQUE_L"], [lo,hi])

    #alternative approach to move_to_encoder, except w/ arbitrary angle setting
    def move_angle(self, ang, angvel=None, blocking=True):
        ''' move to angle (radians)
        '''
        if angvel == None:
            angvel = self.settings['max_speed']

        if angvel > self.settings['max_speed']:
            print( 'lib_robotis.move_angle: angvel too high - %.2f deg/s' % (math.degrees(angvel)))
            print( 'lib_robotis.ignoring move command.')
            return

        if ang > self.settings['max_ang'] or ang < self.settings['min_ang']:
            print( 'lib_robotis.move_angle: angle out of range- ', math.degrees(ang))
            print( 'lib_robotis.ignoring move command.')
            return

        self.set_angvel(angvel)

        if self.settings['flipped']:
            ang = ang * -1.0
        enc_tics = int(round( ang / self.settings['rad_per_enc'] ))
        enc_tics += self.settings['home_encoder']
        self.move_to_encoder( enc_tics )

        if blocking == True:
            while(self.is_moving()):
                continue

    def move_to_encoder(self, n):
        ''' move to encoder position n
        '''
        # In some border cases, we can end up above/below the encoder limits.
        #   eg. int(round(math.radians( 180 ) / ( math.radians(360) / 0xFFF ))) + 0x7FF => -1
        n = min( max( n, 0 ), self.settings['max_encoder'] )
        hi,lo = int(n / 256), int(n % 256)
        return self.write_address( self.ADDR_DICT["ADDR_GOAL_POSITION_L"], [lo,hi] )

    #ADDED: reading the goal encoder position that the user has specified
        #useful for slow motions or torque-limited motions to find distance to goal
    def read_goal(self):
        data = self.read_address( self.ADDR_DICT["ADDR_GOAL_POSITION_L"], 2)
        enc_val = data[0] + data[1] * 256
        return enc_val

    #ADDED: enabling torque control mode for the MX-64 series and above ONLY:
    def enable_torque_mode(self):
        if self.series=='MX':
            return self.write_address(self.ADDR_DICT["ADDR_TORQUE_CONTROL_MODE_ENABLE"], [1])
        else:
            return 0
    def disable_torque_mode(self):
        if self.series=='MX':
            return self.write_address(self.ADDR_DICT["ADDR_TORQUE_CONTROL_MODE_ENABLE"], [0])
        else:
            return 0
    def apply_torque(self,amnt):
        if self.series=='MX':
            amnt = max(0.,min(abs(amnt),1.0))
            torque_val = int(amnt*1023)
            if torque_val < 0:
                torque_val = torque_val+1024
            hi,lo = int(torque_val / 256), int(torque_val % 256)
            return self.write_address(self.ADDR_DICT["ADDR_GOAL_TORQUE_L"],[lo,hi])
        else:
            return 0

    #disabling/enabling address 18 effectively shuts down motor output
        #different from torque mode that's available in the MX models
        #USE ONLY AS ON/OFF quick shutdown control
    def enable_torque(self):
        return self.write_address(self.ADDR_DICT["ADDR_TORQUE_ENABLE"], [1])

    def disable_torque(self):
        return self.write_address(self.ADDR_DICT["ADDR_TORQUE_ENABLE"], [0])

    #same as apply_speed, except set rad/sec as opposed to single value scalar
    def set_angvel(self, angvel):
        ''' angvel - in rad/sec
        '''
        rpm = angvel / (2 * math.pi) * 60.0
        angvel_enc = int(round( rpm / 0.111 ))
        if angvel_enc<0:
            hi,lo = int(abs(angvel_enc) / 256 + 4), int(abs(angvel_enc) % 256)
        else:
            hi,lo = int(angvel_enc / 256),int( angvel_enc % 256)

        return self.write_address( self.ADDR_DICT["ADDR_MOVING_SPEED_L"], [lo,hi] )

    def write_id(self, id):
        ''' changes the servo id
        '''
        return self.write_address( self.ADDR_DICT["ADDR_ID"], [id] )

    def __calc_checksum(self, msg):
        chksum = 0
        for m in msg:
            chksum += m
        chksum = ( ~chksum ) % 256
        return chksum

    def ping(self):
        return self.read_address(self,self.ADDR_DICT["ADDR_MODEL_NUMBER_L"],nBytes=1)

    def read_address(self, address, nBytes=1):
        ''' reads nBytes from address on the servo.
            returns [n1,n2 ...] (list of parameters)
        '''
        msg = [ 0x02, address, nBytes ]
        return self.send_instruction( msg, self.servo_id )


    def write_address(self, address, data):
        ''' writes data at the address.
            data = [n1,n2 ...] list of numbers.
            return [n1,n2 ...] (list of return parameters)
        '''
        msg = [ 0x03, address ] + data
        return self.send_instruction( msg, self.servo_id )

    def send_instruction(self, instruction, id):
        time.sleep(self.return_delay)	#helps w/ communication consistency?

        msg = [ id, len(instruction) + 1 ] + instruction # instruction includes the command (1 byte + parameters. length = parameters+2)
        chksum = self.__calc_checksum( msg )
        msg = [ 0xff, 0xff ] + msg + [chksum]
        self.dyn.acq_mutex()
        try:
            self.send_serial( msg )
            data, err = self.receive_reply()
        except Exception as inst:
            self.dyn.rel_mutex()
            raise RuntimeError(repr(str(inst)))
        self.dyn.rel_mutex()

        if err != 0:
            self.process_err( err )

        return data

    def process_err( self, err ):
        raise RuntimeError('lib_robotis: An error occurred: %d\n' % err)

    def receive_reply(self):
        start = self.dyn.read_serial( 2 )	#from pydynamixel: possible that these contain empty bytes
        servo_id = self.dyn.read_serial( 1 )

        while servo_id=='\xff':
            servo_id = self.dyn.read_serial( 1 )	#on Sparkfun USB-to-RS485 chip, more than 3 header bytes are sometimes set - apparently not an issue with the USB2Dynamixel

        if len(servo_id)!=1:
            raise RuntimeError('lib_robotis: Invalid message headers, got servo id of type: '+repr(type(servo_id))+' and length: '+repr(len(servo_id)))
        if ord(servo_id) != self.servo_id:
            raise RuntimeError('lib_robotis: Incorrect servo ID received')

        data_len = self.dyn.read_serial( 1 )
        err = self.dyn.read_serial( 1 )

        data=[]
        for i in range(ord(data_len)-2):
            input = self.dyn.read_serial( 1 )
            data.append(ord(input))

        checksum = self.dyn.read_serial( 1 ) 		#checksum is read but never compared...(by design, according to original lib_robotis.py)
        return data, ord(err)

    def send_serial(self, msg):
        """ sends the command to the servo
        """
        self.dyn.send_serial( msg )

##################################################################################################

# Class for Model XL Servos

##################################################################################################
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

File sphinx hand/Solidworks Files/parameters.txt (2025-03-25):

"R1vert_ang"= 55deg

"Rsph"= 100mm

"R1R2_dist"= 70mm

"R2S_dist"= 70mm

"BaseAng1"= 90deg

"BaseAng2"= 210deg

"BaseAng3"= 330deg

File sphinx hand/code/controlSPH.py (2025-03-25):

## Control Code for Sphinx Hand

from time import sleep
import lib_robotis_mod as lib

import numpy as np
from random import randint
import math

import sympy as sym

import matlab.engine
eng = matlab.engine.start_matlab()


class SPH:
    def __init__(self):
        # Design Parameters
        self.CC = np.zeros((1,3))               # Fixed common center [mm]
        self.L1 = 70                            # Link 1 length [mm]
        self.L2 = 70                            # Link 2 length [mm]
        self.R1ang = 55*np.pi/180               # Angle of R1 axis from vertical [rad]          
        self.Rsph = 100                         # Spherical motion radius [mm]

        self.L_R2 = np.sqrt(self.Rsph**2 - self.L2**2)    # Distance from center to R2 joint [mm]
        self.L_R1 = np.sqrt(self.L_R2**2 - self.L1**2)    # Distance from center to R1 joint [mm]
        
        self.beta = None                    # active R2 joint position [rad, 3x1]
        self.alpha = None                   # active R1 joint position [rad, 3x1]

        self.initial_alpha = [90*np.pi/180, 90*np.pi/180, 90*np.pi/180]
        self.initial_beta = [-110*np.pi/180, -110*np.pi/180, -110*np.pi/180]

        self.baseAngles = [90*np.pi/180, 210*np.pi/180, 330*np.pi/180]

        self.R = None                               # Object rotation matrix
        self.PP = np.zeros((3,3))                   # R1 joint locations
        self.NN = np.zeros((3,3))                   # Contact locations
        self.NN_grasp = np.zeros((3,3))             # Contact locations at grasp

        self.motTOang = [0, 0, 0, 0, 0, 0]
        self.motTOang[0] = 98*np.pi/180             # Offset from X motor to alpha angle [rad] (keep motors in range +/-180)
        self.motTOang[1] = 78*np.pi/180
        self.motTOang[2] = 70*np.pi/180
        self.motTOang[3] = 0*-180*np.pi/180            # Offset from XL motor to beta angle [rad] (keep motors in range +/-150)
        self.motTOang[4] = 0*-180*np.pi/180
        self.motTOang[5] = 0*-180*np.pi/180

        dyn1 = lib.USB2Dynamixel_Device('COM7')      # '/dev/ttyUSB0'
        dyn2 = lib.USB2Dynamixel_Device('COM8')

        self.XM1 = lib.Robotis_Servo_X(dyn1, 1)     # Initializing XM motors for alpha joints
        self.XM2 = lib.Robotis_Servo_X(dyn1, 2)
        self.XM3 = lib.Robotis_Servo_X(dyn1, 3)

        self.XL1 = lib.Robotis_Servo_X(dyn2, 4)    # Initializing XL-430 motors for beta joints
        self.XL2 = lib.Robotis_Servo_X(dyn2, 5)
        self.XL3 = lib.Robotis_Servo_X(dyn2, 6)

        print('SPH object created.')
        

    # FUNCTION DEFINITIONS

    def initHand(self):
        for f in range(3):
            self.PP[:,f] = np.transpose([self.L_R1*np.sin(self.R1ang)*np.cos(self.baseAngles[f]), 
                                    self.L_R1*np.sin(self.R1ang)*np.sin(self.baseAngles[f]),
                                     -self.L_R1*np.cos(self.R1ang)])

        self.homeHand()
        print('Hand initiated.')


    def homeHand(self):
        alpha_home = self.initial_alpha
        beta_home = self.initial_beta

        self.moveMotors(alpha_home, beta_home, 2.5)

    def openHand(self):                         # different from homeHand() to be able to control speed_a and speed_b
        vals = np.zeros(6)
        for i in range(3):
            vals[i] = (- self.initial_alpha[i] + self.motTOang[i])
            vals[i+3] = (- self.initial_beta[i] + self.motTOang[i+3])

        speed_b = 0.3                       # speed of beta motors: range [0,1]
        self.XL1.set_velprofile(speed_b)
        self.XL2.set_velprofile(speed_b)
        self.XL3.set_velprofile(speed_b)
        
        self.XL1.move_angle(vals[3], blocking=False)
        self.XL2.move_angle(vals[4], blocking=False)
        self.XL3.move_angle(vals[5], blocking=False)

        speed_a = 0.04
        self.XM1.set_velprofile(speed_a)
        self.XM2.set_velprofile(speed_a)
        self.XM3.set_velprofile(speed_a)

        self.XM1.move_angle(vals[0], blocking=False)
        self.XM2.move_angle(vals[1], blocking=False)
        self.XM3.move_angle(vals[2], blocking=False)

        

    def graspHand(self):

        graspTorque = [0.3, 1]      # Range:0-1.0, Increment by max 0.05, Ok up to 0.2-0.3 for XM
        maxCloseAng = [0, 0, 0, 0, 0, 0]                            # Maximum angle motors can close
        alpha0 = [28.1, 34.1,   38.4,   41.5,   63.1,   66.6,   81.5,   87.3]    # for R0.2 to R0.9 objects
        beta0 = [-38.1,-49.8,  -60.3,  -70.5,  -72.5,  -84.3,  -85.7,  -79.5]    # for R0.2 to R0.9 objects
        
        squeezeR = 0.7      # To change approx how hard to squeeze object (radius of "squeezed" object)
        
        squeezeR = int((squeezeR - 0.19)*10)     # convert to index of alpha0 and beta0
        print(squeezeR)
        for i in range(3):
            maxCloseAng[i] = - alpha0[squeezeR]*np.pi/180 + self.motTOang[i]
            maxCloseAng[i+3] = - (beta0[squeezeR]*np.pi/180) + self.motTOang[i+3]

        # setting XM torque limit for grasping, then commanding motors to end of range
        self.XM1.enable_current_position_control_mode(torque_val = graspTorque[0])
        self.XM2.enable_current_position_control_mode(torque_val = graspTorque[0])
        self.XM3.enable_current_position_control_mode(torque_val = graspTorque[0])

        # setting max velocity XM motors can reach
        self.XM1.set_velprofile(0.1)
        self.XM2.set_velprofile(0.1)
        self.XM3.set_velprofile(0.1)
        self.XM1.move_angle(maxCloseAng[0], blocking=False)
        self.XM2.move_angle(maxCloseAng[1], blocking=False)
        self.XM3.move_angle(maxCloseAng[2], blocking=False)

        
        self.XL1.set_velprofile(0.2)
        self.XL2.set_velprofile(0.2)
        self.XL3.set_velprofile(0.2)
        
        
        # Move XL motors only while XM is still moving
        while ((self.XM1.is_moving() or self.XM2.is_moving()) or self.XM3.is_moving()):
            if self.XM1.is_moving():
                self.XL1.move_angle(maxCloseAng[3], blocking=False)
            else:
                self.XL1.move_to_encoder(self.XL1.read_encoder())
            if self.XM2.is_moving():
                self.XL2.move_angle(maxCloseAng[4], blocking=False)
            else:
                self.XL2.move_to_encoder(self.XL2.read_encoder())
            if self.XM3.is_moving():
                self.XL3.move_angle(maxCloseAng[5], blocking=False)
            else:
                self.XL3.move_to_encoder(self.XL3.read_encoder())
            # print("grasping")


        self.R = np.identity(3)
        self.NN_grasp = self.calcNN()

        return True
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

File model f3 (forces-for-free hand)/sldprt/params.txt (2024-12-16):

"Lp" = 54.50
"Ld" = 46.50
"Kp" = 2.80
"Kd" = 3.80
"Kp Length" = 10
"Kd Length" = 10
"Rp" = 8
"Rd" = 7.20
"height" = 18
"depth" = 31.75
"Lb" = 77.50
"Lb Pivot" = 60
"pad thickness" = 4.50
"Tp" = 15
"Td" = 60
"base depth" = 44.45
"width destroy" = 0.7
"width keep" = 3
"width tab" = 4
"print fit" = 0.15
"print free" = 0.35
"pin diameter" = 3.18
"bearing pin diameter" = 3
"pulley diameter" = 9.50
"bearing diameter" = 11
"pulley thickness" = 2.40
"base pin diameter" = 6.35

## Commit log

2015-02-09 Initial upload
    Version 1.0 for the following hand designs: Model T, Model T42, Model O,
    Model M2, Model M
    [3434T31 - nylon pulley.SLDPRT, 90145A421 D1-16 L5-8.SLDPRT, 90480A003 2-56 nut.SLDPRT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]
2015-02-11 Updating stl list for Model O
    [91292A003 M2 L3 socket.SLDPRT, b2_o.SLDPRT, b2_o.STL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]
2015-02-14 PR2 mount update
    added the hard-stop tab to the PR2 mount for OpenHand
    [Mount_PR2.SLDPRT, Mount_PR2.STL]
2015-02-18 Solidworks reference fix
    Updated the appropriate file references in the source Solidworks CAD
    files
    [a1_f_t.SLDPRT, a1_o.SLDPRT, a1_t42.SLDPRT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]
2015-02-18 complete Solidworks configuration set
    expanded the set of available configurations in each assembly file to
    more comprehensive, including both finger type and servo type so that
    you don't have to manually select the configuration of sub-assemblies
    [a1_t42.SLDPRT, a2_m.SLDPRT, a2_t42.SLDPRT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]
2015-02-22 Post Model M CAD update
    binary update after last set of Model M revisions and cleanup
    [91253A106 4-40 L1-4 countersunk.SLDPRT, 91290A012 M2 L5 socket.SLDPRT, 91292A012 M2.5 L8 socket.SLDPRT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]
2015-02-23 Model M2 Distal Link Edit
    Properly implementing the parallel return spring for the M2 gripper
    finger, which is different from the M and T42 setup
    [block_actuator_t42.SLDASM, d1_t42_fan.SLDPRT, finger_pp_A_m2.STL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]
2015-02-23 Model M2 cleanup
    Post documentation re-upload of binaries for Model M2
    [a2_t42.SLDPRT, a3_t42.SLDPRT, block_actuator_t42.SLDASM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]
2015-02-23 Model T42 cleanup
    Updating CAD binaries for Model T42 after completing assembly guide
    documentation
    [a1_t42.SLDPRT, block_actuator_t42.SLDASM, block_finger_ff_t42.SLDASM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]
2015-02-24 Model O cleanup
    Post-documentation update of CAD binaries for Model O
    [90480A003 2-56 nut.SLDPRT, 91253A110 4-40 L1-2 countersunk.SLDPRT, 91292A003 M2 L3 socket.SLDPRT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]
2015-02-24 Model T cleanup
    Post documentation refresh of CAD binaries for the Model T, including
    some stl additions for the shell
    [a1_f_t.SLDPRT, a1_p_t.SLDPRT, a2_t.SLDPRT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]
2015-02-24 Readme Update
    Added link to CAD guide, clarification for using the hardware source
    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
2015-02-28 STEP file addition
    Adding step files for the major hand designs. Binary files also updated
    during export process.
    [a1_f_t.STEP, a1_f_t42.STEP, a1_m.STEP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]
2015-02-28 eDrawings for Model T
    forgot to upload the eDrawings files for the Model T. Extra details
    about use of eDrawings also added to hardware ReadMe
    [block_finger_pp_t.SLDASM, block_top_pp_t.SLDASM]
2015-03-06 UR Coupling update
    holes for Universal Robotics wrist mount were incorrect with diameter
    60mm. Should have been 50mm. Unfortunately, this means that there are
    only 2 mounting holes instead of the standard 4 to make the spacing work
    with this particular dovetail design
    [Mount_UR.SLDPRT, Mount_UR.STL]
2018-08-21 Model C
    Model C v1 added to the repository
    [3310c-101 - Potentiometer.SLDPRT, 3434T310 - Small Idler Pulley - 0.375in.SLDPRT, 57155K375 - Ball Bearing - 0.25in.SLDPRT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]
2019-01-04 model vf parts
    [Friction_Finger_Front_V5.2a_flip.stl, Friction_Finger_Front_V5.2a_servo.stl, Mold_insert_for_FingerV5_v2.stl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]
2019-04-01 version 1.1 model vf
    [Friction_Finger_Front_V5.2a_flip.stl, Friction_Finger_Front_V5.2a_servo.stl, Mold_Base_V3.STL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]
2019-07-01 added model q
    [3434T31 - nylon pulley.SLDPRT, 90480A003 2-56 nut.SLDPRT, 91253A106 4-40 L1-4 countersunk.SLDPRT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]
2019-07-16 xm motors for model t and model o
    [93330A483 8-32 L2 standoff.SLDPRT, a1_f_t.SLDPRT, a1_f_t.STEP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]
2019-08-22 documentation, readme, xm motors on remainng hands
    [93330A450 8-32 L2 standoff.SLDPRT, 94180A333 M3 insert.SLDPRT, 97395A439 D1-8 L1-4.SLDPRT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]
2019-09-23 updated links
    [a1_o.SLDPRT, a1_p_t.SLDPRT, a3_t42.SLDPRT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]
2020-08-24 update hands
    [3310c-101 - Potentiometer.SLDPRT, 3434T310 - Small Idler Pulley - 0.375in.SLDPRT, 57155K375 - Ball Bearing - 0.25in.SLDPRT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]
2021-03-24 model c to openhand
    [3310c-101 - Potentiometer.SLDPRT, 3434T310 - Small Idler Pulley - 0.375in.SLDPRT, 57155K375 - Ball Bearing - 0.25in.SLDPRT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]
2021-03-30 renamed model c
    [3310c-101 - Potentiometer.SLDPRT, 3434T310 - Small Idler Pulley - 0.375in.SLDPRT, 57155K375 - Ball Bearing - 0.25in.SLDPRT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]
2024-12-16 Add F3 hand
    Upload models and guide for Forces for Free (F3) hand.
    [7804K126_Stainless Steel Ball Bearing.SLDPRT, 91595A138_Dowel Pin.SLDPRT, BOM.xlsx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]
2024-12-17 Add assembly guide for Model F3
    [BOM.xlsx]
2025-01-01 Update readme to include model F3
    [7804K126_Stainless Steel Ball Bearing.SLDPRT, 91595A138_Dowel Pin.SLDPRT, F3_finger.SLDPRT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]
